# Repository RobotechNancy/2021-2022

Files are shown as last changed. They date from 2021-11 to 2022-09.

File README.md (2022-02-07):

**`ROBOTECH 2021-2022`** 

## **`DÉPÔT OFFICIEL`**  ##

Dépot officiel 2021-2022 de l'équipe Robotech Nancy pour le projet Coupe de France de Robotique

Après de nombreuses années à explorer les quatre coins du monde et de l’univers, nos amis les robots ont

décidé d’aller explorer leur passé. En 2022, les robots iront fouiller les ruines d’une ancienne civilisation robo-
tique à la recherche des fragments oubliés de leurs origines.

Carré de fouille, trésors enterrés et statuettes sacrées, voilà ce qui attend nos archéologues chevronnés, et
rien ne les arrêtera dans la quête de leur Histoire.
Alors sortez les pelles et les pioches, car l’aventure nous attend !

## **`Devise :`** ##
*L’utilsation optimale de l’énergie est une base élémentaire
dans l’ensemble de nos conceptions.
Savoir optimiser l’utilisation des robots existant ne nous satisfait pas.
Nous voulons apprendre à concevoir les robots de demain
utilisant des technologies novatrices ainsi qu’une 
intelligence réelle supportée par une électronique et une informatique de haut niveau.*

Nos objectifs de cette année sont :

- Construire les 2 robots nécessaires dans la version 2022 de la compétition.
- Consolider la structuration en blocs fonctionnels indépendants ( Base roulante, Odométrie, partie robotique annuelle spécifique, Introduction des services de maintenance, … ).
- Rendre les codes informatiques d’un très haut niveau de qualité ( Méthodologique, Fiables ( traitant de toutes erreurs), réelle documentation professionnelle, … ).
- Cette année nous souhaitons introduire les Graphes et moteur de Graphe afin de rendre plus facile et fiable les évolutions de la compétition tant pour cette année et surtout les années à venir.
- Introduire l’utilisation des technologies WEB dans les logiciels d’Interface Homme Robot.
- Consolider les communications hertziennes entre nos deux robots collaboratifs afin d’introduire l'immunité aux attaques de cyber-sécurité.



## **`EQUIPE DE L'ANNEE 2021-2022`**  ##



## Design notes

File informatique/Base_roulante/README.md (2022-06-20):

Sur la Raspy
- fichiers calculDeplacement

Sur STM
- projet STM BR_L432KCU3_V

Pour paramétrer la STM (timer, DMA) et explications générales sur la base roulante voir Rapport_technique_base_roulante

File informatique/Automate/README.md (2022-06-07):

# Ce code permet de :

- Commander un actionneur type servomoteur à angle
- Commander un actionneur type TOR (electroaimant,pompe,etc)
- Commander un actionneur type moteur PAP 

### L'entièreté des codes sont réalisés sur STM32CUBEIDE Version: 1.9.0    Build: 12015_20220302_0855 (UTC) en langage C/C++

### Pour commander un actionneur type servomoteur à angle : 

1. Créer le projet STM sur LA BONNE VERSION de la carte !!
2. Commencer par configurer les pins de la carte sur le .ioc (pin d'envoie de signal et autres si besoin)
> Un servomoteur à angle à besoin en plus du signal d'être (en général) relié à la masse et au 5V (vérifier sur datasheet si la STM suffit pour l'alimenter ou si il faut rajouter une alimentation externe)
3. Regler ensuite les timers pour bien les calibrer (adapter les valeurs des timers en fonction de la valeur de la clock de l'année)
4. Une fois ces 3 actions effectuer, pour faire fonctionner le servomoteur il faut :
    1. Activer la pin configurée précédemment
    2. Régler la valeur du CCR associé au timer en fonctione de l'angle que l'on veut (faire des tests pour trouver la bonne valeur)
    3. Désactiver la pin une fois l'action du servomoteur effectuée
> Attention une fois une commande d'angle lancée, ne pas bloquer et/ou pousser le servomoteur dans le sens inverse cela risque de le casser/dérégler
> Si il y à besoin d'une fonction d'attente, regarder la fonction faite  à la main dans le projet STM et ne pas utiliser la fonction HAL_DELAY de STM, pendant son utilisation, plus rien d'autre ne se passe.

### Pour commander un actionneur type TOR : 

1. Créer le projet STM sur LA BONNE VERSION de la carte !!
2. Commencer par configurer les pins de la carte sur le .ioc (pin d'envoie de signal et autres si besoin)
> Pour un actionneur TOR, il faut configurer dans GPIO output le GPIO mode en Push Pull sans pull-up ni pull-down (voir avec le pole electronique si la carte alimente l'actionneur en push/pull ou en open-drain)
3. Une fois cela configuré, il suffit d'écrire sur la PIN 1 ou 0 (SET ou RESET) pour activer/désactiver l'actionneur (si en open drain, les commandes sont inversées)
> Pour un actionneur TOR, il faudra très souvent brancher l'actionneur sur une alimentation  externe car la STM ne suffira probablement pas

### Pour commander un actionneur type PAP :

Si besoin d'aide supplémentaire sur les  actionneurs, me contacter par mail rey.thibault@orange.fr ou par discord Thibolt#3886 (voir le discord robotech si besoin).

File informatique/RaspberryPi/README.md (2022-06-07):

# Tutoriel pour implémenter un point d'accès sans fil sur une RaspberryPi

##### Utilité du point d'accès :

Le point d'accès d'une RaspberryPi permet de pouvoir créer un réseau sans fil directement sur la carte sans avoir besoin qu'elle se connecte à un partage de connexion distant pour y accéder.

Cette fonction est particulièrement utile lorsqu'on a besoin de se connecter à plusieurs à une RaspberryPi ou lorsqu'on se trouve dans un endroit sans possibilité d'effectuer un point d'accès autre.

```
/!\ Attention : Ce tutoriel ne permet pas d'effectuer le routage de la connexion internet via la RaspberryPi. 
Le point d'accès sans fil ainsi créé ne permettra pas d'accéder à internet ! 

Une solution est de mettre en place un partage de connexion via USB en branchant son téléphone à la RaspberryPi 
via USB et en sélectionnant l'option "Modem USB" dans les paramètres de connexion.
```

##### Mise en place du point d'accès :

On vérifie tout d'abord que le système est bien à jour, et on installe les paquets nécessaires :

```bash
sudo apt update -y && sudo apt upgrade -y 
```
```bash
sudo apt install hostapd dnsmasq -y
```

On effectue ensuite les configurations nécessaires :

```bash
sudo systemctl stop hostapd dnsmasq
```

```bash
sudo nano /etc/hostapd/hostapd.conf
```

On ajoute le code suivant à la fin du fichier :
```
interface=wlan0
driver=nl80211
ssid=robotechnancygrand
hw_mode=g
channel=7
wmm_enabled=0
macaddr_acl=0
auth_algs=1
ignore_broadcast_ssid=0
wpa=2
wpa_passphrase=Robotech2022@
wpa_key_mgmt=WPA-PSK
wpa_pairwise=TKIP
rsn_pairwise=CCMP
```

```bash
sudo systemctl unmask hostapd && sudo systemctl enable hostapd
```

```bash
sudo nano /etc/default/hostapd
```

On décommente la ligne et on la complète comme ceci :

```
DAEMON_CONF="/etc/hostapd/hostapd.conf"
```

```bash
sudo nano /etc/dnsmasq.conf
```

On ajoute le code suivant à la fin du fichier :

```
interface=wlan0
domain-needed
bogus-priv
dhcp-range=192.168.50.150,192.168.50.200,255.255.255.0,12h
```

```bash
sudo nano /etc/dhcpcd.conf
```

On ajoute le code suivant à la fin du fichier :

```
interface wlan0
nohook wpa_supplicant
static ip_address=192.168.50.10/24
static routers=192.168.50.1
```

On redémarre la RaspberryPi :

```bash
sudo reboot
```

##### Connexion au point d'accès :

- Connexion au wifi généré par la RaspberryPi **[mot de passe : Robotech2022@]**
- Connexion en ssh
```
ssh pi@192.168.50.10 
```
**[mot de passe : robotech2022]**

##### Désactivation du point d'accès :

```bash
sudo nano /etc/dhcpcd.conf
```

Commenter les lignes suivantes (à la fin du fichier) :

```bash
#interface wlan0
#nohook wpa_supplicant
#static ip_address=192.168.50.10/24
#static routers=192.168.50.1
```

On désactive les services réseaux :

```bash
sudo systemctl disable dnsmasq hostapd
```

On redémarre la RaspberryPi :

```bash
sudo reboot
```

##### Réactivation du point d'accès :

```bash
sudo nano /etc/dhcpcd.conf
```

Décommenter les lignes suivantes (à la fin du fichier) :

```bash
interface wlan0
nohook wpa_supplicant
static ip_address=192.168.50.10/24
static routers=192.168.50.1
```

On réactive les services réseaux :

```bash
sudo systemctl enable dnsmasq hostapd
```

On redémarre la RaspberryPi :

```bash
sudo reboot
```

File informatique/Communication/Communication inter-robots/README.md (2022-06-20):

# Le code permet de réaliser :

- la communication inter-robots via XBee (envoi/réception de trames)
- le paramétrage des modules XBee en UART via le port GPIO de la RaspberryPi 

> *Remarque :* Tous les codes sont écrits en style **C/C++**

# Format de la trame des messages envoyés et reçus :

|Début de trame|Adr_emetteur|Adr_destinataire|Id_trame|Nb octets msg|Code_fonction|Paramètres|CRC16 Modbus|Fin de trame|
|:---:|:---:|:---:|:---:|:---:|:---:|:---:|:---:|:---:|
|*1 octet*|*1 octet*|*1 octet*|*2 octets*|*1 octet*|*1 octet*|*<255 octets*|*2 octets*|*1 octet*|
|STX|0xXX|0xXX|0xXX 0xXX|0xXX|0xXX|DATA|0xXX 0xXX|EOT|

> *Remarque :* Tous les codes et adresses nécessaires pour la trame sont définis dans le fichier **#xbee_define.h**

# Principales caractéristiques des connexions mises en oeuvre :

|Nom de la communication|Vitesse de transfert|Portée|Type de communication|Caractéristiques de transmission utilisés (série)|Bande(s) de fréquence
|:---:|:---:|:---:|:---:|:---:|:---:|
|Module XBee type S1|RF : 250Kbps - série: jusqu'à 250Kbps|60m (intérieur) - 90m (extérieur)|Sans fil - Haute Fréquence|9600 bauds - Bit de parité pair - 1 bits de stop - 8 bits de data - chiffrement AES 128 Bits|2,4 GHz avec étalement de spectre|
|Liaison UART|9600 - 115200 bauds|/|Filaire|9600 bauds - Bit de parité pair - 1 bits de stop - 8 bits de data|/|

> Plus d'informations sur le module Digi Xbee 3 DigiMesh 2.4 RF [ici](https://www.digi.com/products/embedded-systems/digi-xbee/rf-modules/2-4-ghz-rf-modules/xbee3-digimesh-2-4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), sur le module XBee S1 [ici](https://www.digi.com/resources/documentation/Digidocs/90000982/Default.htm) ou directement sur la [datasheet du module](https://www.digi.com/resources/library/data-sheets/ds_s2c-xbeedigimesh-24)

# Installation du code (sous Linux x86-64) :

```bash
git clone https://github.com/RobotechNancy/2021-2022.git
```

[**Username** : votre nom d'utilisateur GitHub] 

[**Password** : vous devez générer un personal access token dans `Github -> Settings -> Developer Settings -> Personal Access Token -> Generate new token`]

```bash
cd 2021-2022/Pôle\ informatique/Communication/Communication\ inter-robots/xbee/  

g++ *.cpp -std=c++17 -pthread -o output

./output
```

# Publication d'une nouvelle version du code (sous Linux x86-64) :

```bash
git pull && git add * && git commit -m "Version XX.XXR" && git push
```

[**Username** : votre nom d'utilisateur GitHub] 

[**Password** : vous devez générer un personal access token dans `Github -> Settings -> Developer Settings -> Personal Access Token -> Generate new token`]

# Câblage des modules XBee avec la RaspberryPi

### Points de vigilance :

- L'alimentation de la RaspberryPi, pour une RaspberryPi3B+ ou modèle antérieur : 5.5V / 2A max. (utilisez une alimentation de la salle C244)
> une sous-alimentation entraine une dégradation notoire de la communication UART : ne pas utiliser de chargeur de téléphone (même charge rapide) !

> un câble USB/Micro USB de mauvaise qualité entraine un fonctionnement erroné

- Le câblage du module XBee :
> ne pas utiliser les 4 pins situés à l'arrière de l'[adaptateur XBee vers DIM](./images/adaptateur_xbee.jpg) -> utiliser les pins situés sur le dessous du support **uniquement**

> vérifier le [GPIO Pinout Diagram](https://pinout.xyz) de votre modèle de Raspberry

> les modules XBee s'alimentent en 3,3V

- La compatibilité entre les modules XBee :
> 2 modules XBee ne sont compatibles que s'ils sont du même type (par ex. les modules XBee S1 et XBee S2C ne sont pas compatibles entre eux)

- En cas d'impossibilité d'accès au module XBee et pour vérifier s'il n'est pas endommagé :
> utiliser le logiciel propriétaire [XCTU](http://www.digi.com/xctu) et connecter le module XBee au port USB de votre ordinateur à l'aide de l'[explorer board XBee](./images/explorer_xbee.jpg)

> dans le logiciel XCTU, cliquez sur l'icône avec la loupe et non celui avec le + pour ajouter un module

- Si vous rencontrez un autre problème, la **meilleure** solution est d'utiliser [un analyseur numérique de signal (ou un oscilloscope)](./images/oscilloscope.jpg), notamment les oscilloscopes digitaux Rohde & Schwarz de la salle C244

### Schéma de câblage :

- Câblage RaspberryPi 3B + Xbee S1 :

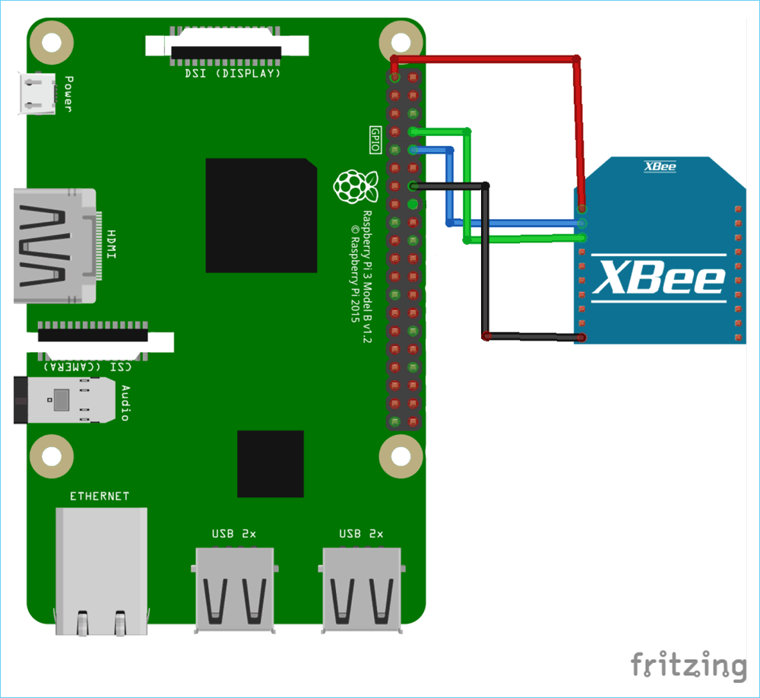
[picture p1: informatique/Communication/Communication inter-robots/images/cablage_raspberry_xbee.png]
Câblage RaspberryPi 3B + Xbee S1


- GPIO Pinout Xbee S1 :

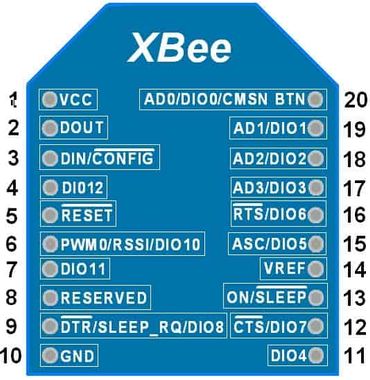
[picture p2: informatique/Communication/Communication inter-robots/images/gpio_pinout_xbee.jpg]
GPIO Pinout Xbee


|**PIN**|**DESCRIPTION**|
|:---:|:---:|
|1|**Alimentation (3,3V)**|
|2|**UART Tx**|
|3|**UART Rx**|
|4|Digital output 8|
|5|Module RESET (pulse reset min. 200ns)|
|6|PWM sortie 0|
|7|PWM sortie 1|
|8|*Ne pas connecter*|
|9|STR / Digital input 8|
|10|**Masse (GND)**|
|11|Analog input 4 / Digital I/O 4|
|12|Clear-to-Send Flow control / Digital I/O 7|
|13|Indicateur d'état du module|
|14|Tension de référence pour les entrées A/D|
|15|Associated Indicator / Analog Input 5 / Digital I/O 5|
|16|Request-to-Send Flow Control / Analog Input 6 / Digital I/O 6|
|17|Analog Input 3 or Digital I/O 3|
|18|Analog Input 2 or Digital I/O 2|
|19|Analog Input 1 or Digital I/O 1|
|20|Analog Input 0 or Digital I/O 0|

- GPIO Pinout RaspberryPi 3B :

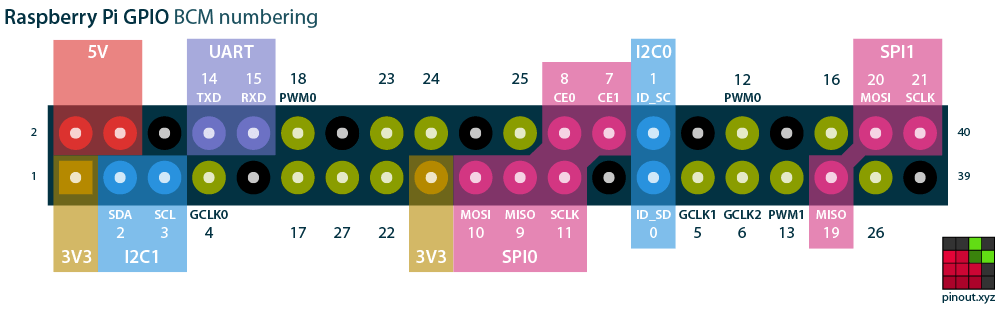
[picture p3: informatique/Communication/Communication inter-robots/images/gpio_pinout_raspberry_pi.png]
GPIO Pinout RaspberryPi


> Les pins dessinés en noir non légendés représentent la masse commune de la Raspberry

- Cablâge ArduinoUno + XBee S1 :

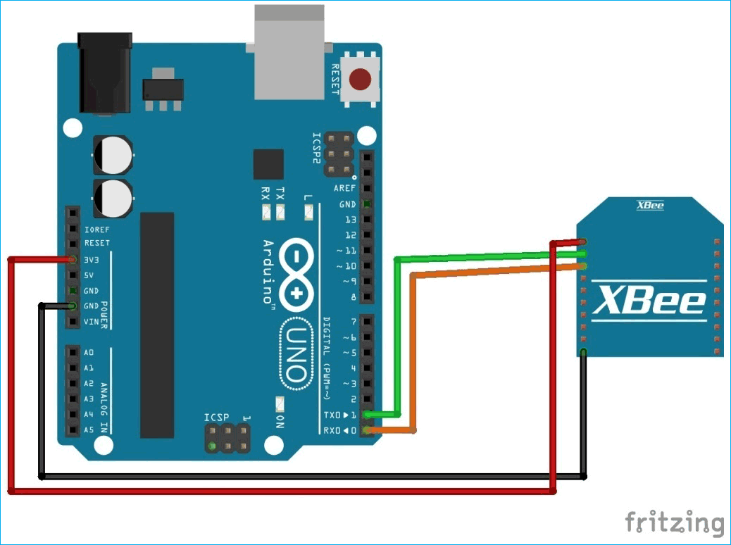
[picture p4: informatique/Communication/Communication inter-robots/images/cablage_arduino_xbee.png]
Cablâge ArduinoUno + XBee S1


# Documentation du code :

- toute la documentation a été générée grâce à l'outil [Doxygen](https://www.doxygen.nl/index.html)
- le fichier de configuration de Doxygen se trouve dans le dossie **xbee** (fichier *Doxyfile*)
- pour consulter la documentation en PDF, ouvrer le fichier **refman.pdf** situé dans le dossier `doc -> latex -> refman.pdf`
- pour consulter la documentation en HTML, ouvrer le fichier **index.html** situé dans le dossier `doc -> html -> index.html`

***
En cas de besoin, contactez moi sur Discord `@heatsink.ru#1183` ou par mail samueldittedestree@protonmail.com

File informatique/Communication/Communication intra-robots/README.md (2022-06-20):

# definition de la trame du bus can

## Champ d'identification en version étendu (29 bit)
| msg urgent | desitnataire | emetteur | code fct |  id msg  | reponse ou question | id rep |
| --- | --- | --- | --- | --- | --- | --- |
| 0 | 0001 | 0010 | 00000101 | 00000001 | 0 | 001  |

- msg urgent : 0 pour un message urgent, 1 sinon
- destinataire : addresse du destinataire du message sur 4 bit (0 à 15)
- emetteur : addresse de l'emetteur du message sur 4 bit (0 à 15)
- code fonction : code fonction du message qui indique a quoi sert le message sur 8 bit (0 à 254)
- id du message : identique entre une demande et une reponse ce qui permet d'idnetifier la réponse, sur 8 bit (0 à 254)
- reponse ou question : un bit , 1 pour une reponse et 0 sinon
- id rep : si des donners doivent etre transmis sur plusieur trame

dans le bus can la prioriter des messages en cas de conflit est donner au message avec le champ d'identification le plus faible.
>ceci implique que les messages sont priorisé par le déstinataire du message

### Adresse des cartes 21-22
| adresse | carte |
| :---: | :---: |
| 1 | raspberry pi |
| 2 | base roulante |
| 3 | odometrie |
| 4 | actionneur |
| 5 | pi zero |
>la pi zero n'a pas était implementé cette année 

# Mise en place du bus can
## Sur la raspberry

installer le packet can-utils : 
```bash
sudo apt install can-utils
```

ajouter le fichier `/boot/config.txt` :
```bash
dtoverlay=mcp2515-can0,oscillator=12000000,interrupt=25,spimaxfrequency=2000000
```
12000000 dépend du quartz utilisé (souvent 12000000 ou 8000000)

il faut lancer cette commande a chaque redémarage de la raspberry :
```bash
sudo ip link set can0 up type can bitrate 181818 loopback off
```
- le bitrate doit etre le meme sur toute les cartes du bus can
- il est possible de passer en **loopback on** ce qui fait que les messages **NE sont PLUS** envoyer dans le bus can mais sont renvoyer sur la carte.
- pour arreter le bus can (et pouvoir le redmarer avec d'autre parametre) : `sudo ip link set can0 down`

## Sur une STM32

Dans le .ioc :
- activer le bus **can1** ou **can**
- dans **Parameter Settings** modifier :
	- **Prescaler (for Time Quantum)**
	- **Time Quanta in Bit Segment 1**
	- **Time Quanta in Bit Segment 2**
de tel sorte d'obtenir le **Baud Rate** voulu (identique autre carte connecter au bus can. 181818 bit/s par example).
Sur une carte en confguration par default :

| PARAMETRE | VALEUR |
| --- | --- |
| **Prescaler (for Time Quantum)** | 16 |
| **Time Quanta in Bit Segment 1** | 8 Times | 
| **Time Quanta in Bit Segment 2** | 2 Times | 

- dans **NVIC Settings** tous cocher !!! (4 cases ou 1 en fonction de la carte)
- verifier que les pin sont bien ascossier comme cela :

| PIN  | DESCRIPTION |
| --- | --- |
| PA12 | CAN1_TX |
| PA11 | CAN1_RX | 
- Inclure les fichiers : can.c, can.h, defineCan.h
- dans le main :
	- include `#include "defineCan.h"` et `#include "can.h"`
	- dans le user code 2 du main mettre 
```c
CAN_Config(hcan1, CAN_ADDR_BASE_ROULANTE_E);
``` 
avec hcan1 la variable de type `CAN_HandleTypeDef` instantier dans private variable, et **CAN_ADDR_BASE_ROULANTE_E** une valeur de l'enum **CAN_EMIT_ADDR**

# Utilisation du bus can
## Sur la raspberry
il existe un certain nombre de commande qui permete d'utilise le bus can :
- **candump can0** permet d'afficher tous les messages qui passe sur le bus can (meme ceux envoyer par la raspberry)
> si les messages envoyer n'apparaissent c'est qu'il n'y a aucune autre carte sur le bus pour accuser reception -> problème de branchement, !! resistance entre canL et canH !!
> si les messages envoyer apparaissent en double -> le loopback est activer, les messages ne sont pas envoyé aux autres cartes

- **cansend can0** permet d'envoyer un messages sur le bus can :
> example de syntaxe : `cansend can0 03132010#12`
> pour information sur l'utilisation de la commande : `cansend` ou `man cansend`

- la librairie possede un grand nombre d'autre commande [cf .doc du packet](https://github.com/linux-can/can-utils)

librairie orienté objet en c++ : voir le dossier [can_raspberry](https://github.com/RobotechNancy/2021-2022/edit/main/P%C3%B4le%20informatique/Communication/Communication%20intra-robots/can_raspberry/)

## Sur une STM32
les messages reçu déclanche une intéruption en appelant la fonction 
```c
void HAL_CAN_RxFifo0MsgPendingCallback(CAN_HandleTypeDef *hcan)
```
pour envoyer un message il faut utiliser 
```c
int send(CAN_ADDR addr, CAN_CODE_FCT codeFct , uint8_t data[], uint dataLen, bool isRep, uint repLenght, uint idMessage)
```

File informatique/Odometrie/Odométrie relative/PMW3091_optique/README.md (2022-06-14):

/////////////////////////////////////////////////////// Utilisation code CAPTEUR OPTIQUE PMW3091 ///////////////////////////////////////////////////////

## DRIVERS : PMW3091.c et PMW3091.h

- Le .c contient les fonctions utilent pour faire fonctionner le capteur correctement et dans le .h on annonce chaque fonction
- Les deux doivent être implémentés dans le projet sous forme de Source Folder
- Il faut ajouter en include les drivers pour que ça marche

## STM32L432K : PMW3091.ioc

- Pour faire fonctionner le reste du code : le port SPI sur la carte STM 32 doit être activé manuellement sur l'IDE de STM 32 en FULL Duplex Master
- ACtiver sur la STM32 les ports SPI1_SCK et en plus un port GPIO_OUTPUT : qu'il faut renommer SPI1_CS
- Au niveau de la connectivité SPI de la carte STM il faut aller dans parameter Settings => 

  - Frame Format : Motorola
  - Data Size : 8 Bits
  - First Bit : MSB First
  - Prescaler (for Baud Rate) : 256
  - Baud Rate : 125 Kbits/s
  - Clock Polarity : Low
  - Clock Phase : 1 Edge
  - CRC Calculation : Disabled
  - NSSP Mode : Enabled 
  - NSS Signal Type : Software
 
 ## Main : main.c 
 
 - Il faut ajouter le PMW3091.h en include
 - Il faut d'abord initialiser le capteur dans le code grâce à la fonction qui le permet (PMW3901_Status_t PMW3901_Init(PMW3901_Descriptor_t *_Descriptor))
 - Si l'initialisation fonctionne les leds du capteur devrait s'allumer
 - Ensuite il faut ajouter la fonction permettant de lire la variation de position du capteur (PMW3901_Status_t PMW3901_Read_Variation(int16_t *var_x, int16_t *var_y))

 ## Résumé 
 
 Le code présent déjà sur le Git permet actuellement de faire fonctionner le capteur optqiue c'est à dire qu'en installant l'application putty et en lancant en parallèle le code, on récupère la variation en x et en y du déplacement du capteur en mm grâce à deux DEFINE qui convertissent les données reçues en mm.
 
 De plus, il permet ensuite de calculer la position relative du capteur : c'est à dire que si le robot bouge il va garder en position initiale l'endroit où il était au démarrage du code et ensuite on le déplacant, on observera sur putty en mm les longueurs qu'il aura parcouru. En le remettant à la position initiale il va redonner posX = 0 et posY = 0 avec un taux d'erreur de lordre du mm.
 
 Le code fonctionne pour les 2 robots que ce soit pour le capteur du petit robot tout comme celui du grand robot. La seule chose qu'il faut modifier entre le petit et le grand robot, c'est les DEFINE en haut du code correspondant au coefficient en X et en Y qu'on doit modifier afin d'ajuster la position du capteur en relatif (directement par rapport au robot).
 
 Lien vers la DATASHEET : 
[Datasheet_CapteurOptique_PMW3901 (2).pdf](https://github.com/RobotechNancy/2021-2022/files/8897904/Datasheet_CapteurOptique_PMW3901.2.pdf)


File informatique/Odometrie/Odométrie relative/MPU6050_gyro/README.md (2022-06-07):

# Le code permet de réaliser :

- la communication en I2C avec le gyroscope
- l'initialisation du gyroscope
- la récupération de la vitesse angulaire, et sa conversion en angle de rotation sur l'axe Z (axe à la verticale du capteur lorque ce dernier est posé à l'horizontal)

> *Remarque :* Le code contenu dans le fichier GYRO_ACC_SAM est l'ensemble du projet réalisé sur l'**IDE STM32** | /!\ Le code **ne permet pas** l'utilisation de l'accéléromètre intégré au capteur

# Utilisation du code :

Pour utiliser le code, il vous faut :

- une carte STM32 disposant au minimum d'un bus I2C et d'une Pin d'interruption
  > le modèle utilisé pour le projet est la STM32L432KCU3 : pour utiliser la librairie sur une autre carte, copier uniquement les fichiers **Core/Inc/Gyro.h**, **Core/Inc/MPU6050.h**, **Core/Src/Gyro.c** ainsi que **Core/Src/MPU6050.c** et créer un nouveau projet STM
  >
- un gyrocope de type MCU6050
  > attention : pour câbler correctement le module, référez-vous à la section ci-après
  >
- avoir installé (sur windows ou linux) l'IDE fourni par STM32 appelé STM32CUBEIDE (disponible [ici](https://www.st.com/en/development-tools/stm32cubeide.html))
- des câbles de connexion et une plaque d'essai (ou un shield adapté)

Les fichiers **Core/Inc/Gyro.h**, **Core/Inc/MPU6050.h**, **Core/Src/Gyro.c** ainsi que **Core/Src/MPU6050.c** ont été écrit à la main, et servent à la configuration du capteur pour notre utilisation. Il se peut que vous soyez ammenés à les modifier, donc voici une courte description de chacun d'entre eux :
  
-> Dossier **Core/Inc** :

- le fichier "*MPU6050.h*" contient le code permettant de configurer les paramètres utilisés pour comminiquer avec le capteur et récupérer les valeurs, et permet également d'inclure la librairie associée à la famille de la carte en cours d'utilisation.

Au début du fichier, on trouve :

```
  #include "stm32l4xx_hal.h"
```

   Pour une autre famille de carte, il suffit de remplacer cette ligne, et de mettre le nom de la famille de la carte. Vous pouvez trouver cette information en regardant le nom du fichier de votre projet situé dans "**Core/Inc/stm32XXXX_hal_conf.h**". Recopier ce nom (sans le *_conf*) dans le fichier à la ligne citée précédemment.
   
  Le reste du fichier contient la configuration du module, avec notamment la posibilité de modifier sa sensibilité, sa vitesse d'horloge, sa fréquence et ses paramètres d'interruptions. Toutes les configurations possibles pour ces paramètres se trouvent *dans les énum des lignes 27 à 119*.  
  
  On trouve ensuite les paramètres en cours d'utilisation, sous forme de 3 structures, situées *entre les lignes 121 et 149*. 
  
  Enfin, on trouve les prototypes des fonctions qui permettent d'initialiser le capteur, et de récupérer la vitesse angulaire fournie par le capteur. Cette vitesse sera ensuite utilisée et traitée par le fichier **Gyro.c**.
  
- le fichier "*Gyro.h*" contient les prototypes des fonctions permettant de gérer la calibration du capteur ainsi que la conversion et le traitement des valeurs de vitesse angulaire afin de fournir la rotation en degrés.  

-> Dossier **Core/Src** :

- le fichier "*MPU6050.c*" contient les fonctions qui permettent d'initialiser le capteur, et de récupérer la vitesse angulaire fournie par le capteur.  

- le fichier "*Gyro.c*" contient les fonctions permettant de gérer la calibration du capteur ainsi que la conversion et le traitement des valeurs de vitesse angulaire afin de fournir la rotation en degrés. Ce fichier est une extension des fonctions contenues dans "*MPU6050.c*", d'où l'inclusion du fichier dans la classe *Gyro*.

Afin d'asssurer le fonctionnement de la librairie, il est nécessaire de modifier légèrement le fichier "*Core/Src/stm32l4xx_it.c*", afin d'ajouter dans la liste des include la libairie `#include "MPU6050.h"`. Il faut également appeler la fonction "*MPU6050_Interrupt_Routine()*" dans la fonction d'interruption système (située à la fin du fichier), pour obtenir un résultat comme ceci :

```c
/**
  * @brief This function handles EXTI line[9:5] interrupts.
  */
void EXTI9_5_IRQHandler(void)
{
  /* USER CODE BEGIN EXTI9_5_IRQn 0 */

  /* USER CODE END EXTI9_5_IRQn 0 */
  HAL_GPIO_EXTI_IRQHandler(GPIO_PIN_6);
  /* USER CODE BEGIN EXTI9_5_IRQn 1 */
  MPU6050_Interrupt_Routine();
  /* USER CODE END EXTI9_5_IRQn 1 */
}
```
> *Remarque :* Les numéros des fonctions par défaut dépendant de la carte utilisée et de la configuration mise en place, et sont donc susceptibles de changer

# Câblage des modules et pinout configuration

Voici le câblage utilisé pour le projet, utilisant 1 capteur MPU6050 et une carte STM32L432KCU3 :

| MPU6050 | STM32L432KCU3 |
| --- | --- |
| GND (masse) | GND (pin CN4-2 ou pin CN3-4) |
| SCL (serial clock) | PA9 |
| SDA (serial data)  | PA10 |
| VIN (alimentation) | +3.3V (pin CN4-14) |

*Les pins situés sur la même ligne sont reliés entre eux*

> Pour configurer le bus I2C sur la carte STM32, il faut penser à activer les réglages de l'interruption du bus, dans le fichier **IOC du projet STM32**, dans le menu **Connectivity>I2C1>NVIC Settings** et cocher l'activation des interruptions **I2C1 event interrupt** et **I2C1 error interrupt** . Il faut ensuite se rendre dans le menu **System Core>GPIO>I2C** et de modifier les 2 lignes du bus I2C en réglant la valeur de **GPIO Pull-Up/Pull-down** sur **Pull-up** (il suffit de double cliquer sur chacune des deux lignes pour faire apparaitre le menu).
>
> Cela permet de ne pas mettre de résistances de Pull-up aux extrémités du bus I2C puisqu'elles sont en réalité internes dans la carte STM32.
> Le mode de l'I2C à utiliser est *I2C*
> Il faut ensuite utiliser une Pin non utilisée (PA6 sur l'IOC dans notre projet) et la régler sur "*GPIO_EXTI6*" afin de l'utiliser par la suite comme Pin d'interruption

Pinout configuration de la carte STM32 NUCLEO-L432KCU3 :

| Numéro de la PIN  | CN3 (partie gauche de la carte) | CN4 (partie droite de la carte) |
| --- | --- | --- |
| 1 | PA9 - D1 (SCL) | VIN |
| 2 | PA10 - D0 (SDA) | GND (masse) |
| 3 | NRST | NRST |
| 4 | GND (masse) | +5V |
| 5 | PA12 - D2 | PA2 - A7 |
| 6 | PB0 - D3 | PA7 - A6 |
| 7 | PB7 - D4 | PA6 - A5 |
| 8 | PB6 - D5 | PA5- A4 |
| 9 | PB1 - D6 | PA4 - A3 |
| 10 | PC14 - D7 | PA3 - A2 |
| 11 | PC15 - D8 | PA1 - A1 |
| 12 | PA8 - D9 | PA0 - A0 |
| 13 | PA11 - D10 | AREF |
| 14 | PB5 - D11 | +3.3V |
| 15 | PB4 - D12 | PB3 - D13 |

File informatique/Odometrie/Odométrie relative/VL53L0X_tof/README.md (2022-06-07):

# Le code permet de réaliser :

- la communication en I2C avec les capteurs TOF
- l'initialisation des capteurs un à un
- la lecture et la conversion des valeurs afin de récupérer des valeurs de distances mesurées en mm

> *Remarque :* Le code contenu dans le fichier TOF_SAM est l'ensemble du projet réalisé sur l'**IDE STM32**

# Utilisation du code :

Pour utiliser le code, il vous faut :

- une carte STM32 disposant au minimum d'un bus I2C et d'un GPIO
  > le modèle utilisé pour le projet est la STM32L432KCU3 : pour utiliser la librairie sur une autre carte, copier uniquement le dossier **Drivers/VL53L0X** et le contenu ***utilisateur*** du fichier **Core/Src/main.c** et créer un nouveau projet STM
  >
- un ou plusieurs capteurs TOF de type VL53L0X (ou VL53LXX)
  > attention : pour câbler correctement les modules, référez-vous à la section ci-après
  >
- avoir installé (sur windows ou linux) l'IDE fourni par STM32 appelé STM32CUBEIDE (disponible [ici](https://www.st.com/en/development-tools/stm32cubeide.html))
- des câbles de connexion et une plaque d'essai

Ce code est basé sur la librairie STM32 qui a été adaptée de manière à être universelle pour toutes les cartes compatibles. La librairie modifiée se trouve dans le dossier **Drivers/VL53L0X.**

Les dossiers **Src** et **Inc** contiennent uniquement des fichiers générés par STM, il ne faut surtout pas les modifier.

Les fichiers commencant par **"TOF_"** et situés dans les dossiers **Implementation** et **Platform** ont été écrit à la main, et servent à l'implémentation du code pour notre utilisation. Il se peut que vous soyez ammenés à les modifier, donc voici une courte description de chacun d'entre eux :

-> Dossier **Implementation** :

- le fichier "*TOF_STM_Reference.h*" contient uniquement le code permettant d'inclure la librairie associée à la famille de la carte en cours d'utilisation.

  ```
  #include "stm32l4xx_hal.h"
  ```

    Pour une autre famille de carte, il suffit de remplacer cette ligne, et de mettre le nom de la famille de la carte. Vous 			pouvez trouver cette information en regardant le nom du fichier de votre projet situé dans "**Core/Inc/stm32XXXX_hal_conf.h**". Recopier ce nom (sans le *_conf*) dans le fichier cité précédemment.

- le fichier "*TOF_STM_Units.h*" contient les informations par défaut des capteurs (adresse I2C, ID de base, mode de relevé de mesure, ...) ainsi que la liste des noms de capteurs TOF utilisés sous forme d'une structure de type *enum*.

  ```
  typedef enum {
  	TOF_UNIT_0 = 0,
  	TOF_UNIT_1 = 1,

  	TOF_UNIT_COUNT // Let this enum value !!!! Mandatory for the driver operations
  } TOF_Units_t;
  ```

    Dans notre exemple, il y deux capteurs TOF listés qui s'appellent respectivement*TOF_UNIT_0* et *TOF_UNIT_1* et qui possèdent les numéros 0 et 1. Pour ajouter un modèle, il suffit de le mettre dans cette liste, et dans le fichier "*TOF_STM_Units.c*" associé.

- le fichier "*TOF_STM_Units.c*" contient les informations détaillées de la liste des capteurs TOF du fichier précédent.
  ```
  VL53L0X_Dev_t TOF_Devices[] = {
  	{
  		.Id = TOF_UNIT_0,
  		.I2cHandle = &hi2c1,
  		.XSHUT_Port = TOF0_XSHUT_GPIO_Port,
  		.XSHUT_Pin = TOF0_XSHUT_Pin
  	},
  	{
  		.Id = TOF_UNIT_1,
  		.I2cHandle = &hi2c1,
  		.XSHUT_Port = TOF1_XSHUT_GPIO_Port,
  		.XSHUT_Pin = TOF1_XSHUT_Pin
  	}
  };
  ```

    Pour chaque module listé dans le fichier .h, on retrouve son ID, l'ID de l'objet I2C (du bus I2C) auquel il est connecté, le nom du port GPIO auquel est connecté la sortie XSHUT du capteur, ainsi que le nom de la Pin qui lui est associée. Pour ajouter un module, il suffit de respecter le format en incrémentant le numéro que le dernier TOF listé possède dans chacune des variables (le même bus I2C étant utilisé pour tous les capteurs, cette variable ne change pas).

> *Remarque importante :* Les capteurs TOF VL53L0X ne possèdent que de la mémoire volatile, et ne retiennent donc pas la nouvelle adresse de bus I2C qui leur est associée. Par défaut, tous les capteurs ont la même adresse, à chaque démarrage, il faut donc tous les éteindre, puis les allumer un à un et leur attribuer une adresse différente entre eux pour pouvoir les distinguer et commiquer avec un à un. C'est tout l'intérêt de la sortie XSHUT du capteur qui signifie XSHUTDOWN, et qui permet d'éteindre les capteurs un à un via le port GPIO de la STM lors de l'initialisation.

    Pour que l'ensemble du code fonctionne, il faut donc que chaque capteur TOF soit relié à une Pin GPIO différente sur la carte STM32. Pour configurer les Pins GPIO sur la carte, il faut repérer sur la carte des Pins non utilisées (*voir la section du câblage pour plus d'informations*), puis se rendre dans le fichier **.ioc** du projet STM32, clic droit sur la Pin choisie, puis sélectionner "GPIO Output" dans la liste déroulante des options. La Pin passe alors à l'état activé et se colore en vert. Il faut ensuite éditer son nom, en effectuant un clic gauche sur la Pin, puis sélectionner "Enter User Label" et indiquer le nom de la Pin sous la forme "TOFX_XSHUT", où le premier X désigne le numéro choisi pour le capteur dans la liste du fichier précédent.

-> Dossier **Platform** :

- le fichier "*TOF_Errors.h*" contient la liste de l'ensemble des codes erreurs qui peuvent être utilisés dans toute la librairie. Leurs noms sont assez explicites, et si on effectue un *Ctrl+clic droit* sur chacune des variables, on peut trouver un commentaire descriptif de l'erreur. Toutefois, si vous souhaitez des descriptions plus précises, vous pouvez consulter le site suivant : [https://documentation.help/VL53L0X-API/](https://documentation.help/VL53L0X-API/)
- le fichier "*TOF_Types.h*" contient les listes des options utilisables pour modifier les paramètres des capteurs, comme le mode de relevé de valeurs, ou encore l'état du capteur.
- les fichiers "*TOF.h*" et "*TOF.c*" contiennent les deux fonctions principales qui sont utilisables par l'utilisateur de la librairie, une première qui permet d'initialiser les capteurs TOF, en paramétrant les registres, et les adresses I2C de chaque capteur, et une seconde qui permet d'effectuer un relevé de la distance fournie par un capteur en mm. D'autres fonctions sont également présentes et sont des fonctions utilitaires internes qui servent aux deux fonctions principales pour mieux découper le programme.

  > Par défaut, les relevés de mesure s'effectuent en mode "LONG_RANGE"
  >

L'ensemble de cette librairie est utilisée dans le fichier **Core/Src/main.c** qui permet d'appeler les fonctions de la librairie, d'initialiser les capteurs, de lire les valeurs envoyées par les capteurs et de transmettre ces valeurs via le bus UART à l'utilisateur afin qu'il puisse vérifier qu'elles sont cohérentes (une valeur de statut est également envoyée à chaque mesure, afin d'indiquer si cette dernière a correctement été effectuée).

# Câblage des modules et pinout configuration

Voici le câblage utilisé pour le projet, utilisant 2 capteurs TOF et une carte STM32L432KCU3 :

| VL53L0X n°1 | VL53L0X n°2  | STM32L432KCU3 |
| --- | --- | --- |
| XSHUT | / | PA6 |
| / | XSHUT | PA5 |
| GND (masse) | GND | GND (pin CN4-2 ou pin CN3-4) |
| SCL (serial clock) | SCL | PA9 |
| SDA (serial data)  | SDA | PA10 |
| VIN (alimentation) | VIN | +3.3V (pin CN4-14) |

*Les pins situés sur la même ligne sont reliés entre eux*

> Pour configurer le bus I2C sur la carte STM32, il faut penser à changer les réglages de la vitesse, dans le fichier **IOC du projet STM32**, dans le menu **Connectivity>I2C1>Parameter Settings** et régler la valeur de **I2C Speed Frequency (KHz)** à 10 (au lieu de 100 par défaut). Il faut ensuite se rendre dans le menu **System Core>GPIO>I2C** et de modifier les 2 lignes du bus I2C en réglant la valeur de **GPIO Pull-Up/Pull-down** sur **Pull-up** (il suffit de double cliquer sur chacune des deux lignes pour faire apparaitre le menu).
>
> Cela permet de ne pas mettre de résistances de Pull-up aux extrémités du bus I2C puisqu'elles sont en réalité internes dans la carte STM32.

Pinout configuration de la carte STM32 NUCLEO-L432KCU3 :

| Numéro de la PIN | CN3 (partie gauche de la carte) | CN4 (partie droite de la carte) |
| --- | --- | --- |
| 1 | PA9 - D1 (SCL) | VIN |
| 2 | PA10 - D0 (SDA) | GND (masse) |
| 3 | NRST | NRST |
| 4 | GND (masse) | +5V |
| 5 | PA12 - D2 | PA2 - A7 |
| 6 | PB0 - D3 | PA7 - A6 |
| 7 | PB7 - D4 | PA6 - A5 |
| 8 | PB6 - D5 | PA5- A4 |
| 9 | PB1 - D6 | PA4 - A3 |
| 10 | PC14 - D7 | PA3 - A2 |
| 11 | PC15 - D8 | PA1 - A1 |
| 12 | PA8 - D9 | PA0 - A0 |
| 13 | PA11 - D10 | AREF |
| 14 | PB5 - D11 | +3.3V |
| 15 | PB4 - D12 | PB3 - D13 |

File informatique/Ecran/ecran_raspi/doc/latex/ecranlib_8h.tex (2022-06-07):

\hypertarget{ecranlib_8h}{}\doxysection{Référence du fichier ecranlib.\+h}
\label{ecranlib_8h}\index{ecranlib.h@{ecranlib.h}}

Fichier d\textquotesingle{}en-\/tête de la classe \mbox{\hyperlink{class_ecran}{Ecran}}. Cette classe est utilisée afin de communique en UART avec l\textquotesingle{}écran sur la Raspberry\+Pi.  

{\ttfamily \#include \char`\"{}ecran\+\_\+define.\+h\char`\"{}}\newline
{\ttfamily \#include \char`\"{}serialib.\+h\char`\"{}}\newline
{\ttfamily \#include \char`\"{}loglib.\+h\char`\"{}}\newline
{\ttfamily \#include $<$string$>$}\newline
{\ttfamily \#include $<$iomanip$>$}\newline
{\ttfamily \#include $<$iostream$>$}\newline
{\ttfamily \#include $<$chrono$>$}\newline
{\ttfamily \#include $<$thread$>$}\newline
{\ttfamily \#include $<$iterator$>$}\newline
\doxysubsection*{Classes}
\begin{DoxyCompactItemize}
\item 
struct \mbox{\hyperlink{struct_trame__t}{Trame\+\_\+t}}
\item 
class \mbox{\hyperlink{class_ecran}{Ecran}}
\begin{DoxyCompactList}\small\item\em Cette classe est utilisée pour la communication entre un ecran STM32\+F7G et une Raspberry\+Pi. \end{DoxyCompactList}\end{DoxyCompactItemize}

\doxysubsection{Description détaillée}
Fichier d\textquotesingle{}en-\/tête de la classe \mbox{\hyperlink{class_ecran}{Ecran}}. Cette classe est utilisée afin de communique en UART avec l\textquotesingle{}écran sur la Raspberry\+Pi. 

\begin{DoxyAuthor}{Auteur}
Samuel-\/\+Charles DITTE-\/\+DESTREE (\href{mailto:samueldittedestree@protonmail.com}{\texttt{ samueldittedestree@protonmail.\+com}}) 
\end{DoxyAuthor}
\begin{DoxyVersion}{Version}
1.\+0 
\end{DoxyVersion}
\begin{DoxyDate}{Date}
31/05/2022 
\end{DoxyDate}

Définition dans le fichier \mbox{\hyperlink{ecranlib_8h_source}{ecranlib.\+h}}.

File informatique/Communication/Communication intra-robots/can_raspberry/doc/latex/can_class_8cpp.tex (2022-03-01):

\hypertarget{can_class_8cpp}{}\doxysection{Référence du fichier can\+Class.\+cpp}
\label{can_class_8cpp}\index{canClass.cpp@{canClass.cpp}}
{\ttfamily \#include $<$stdio.\+h$>$}\newline
{\ttfamily \#include $<$stdlib.\+h$>$}\newline
{\ttfamily \#include $<$string.\+h$>$}\newline
{\ttfamily \#include $<$unistd.\+h$>$}\newline
{\ttfamily \#include $<$iostream$>$}\newline
{\ttfamily \#include $<$net/if.\+h$>$}\newline
{\ttfamily \#include $<$sys/ioctl.\+h$>$}\newline
{\ttfamily \#include $<$sys/socket.\+h$>$}\newline
{\ttfamily \#include $<$linux/can.\+h$>$}\newline
{\ttfamily \#include $<$linux/can/raw.\+h$>$}\newline
{\ttfamily \#include $<$thread$>$}\newline
{\ttfamily \#include \char`\"{}can\+Class.\+h\char`\"{}}\newline
{\ttfamily \#include \char`\"{}define\+Can.\+h\char`\"{}}\newline

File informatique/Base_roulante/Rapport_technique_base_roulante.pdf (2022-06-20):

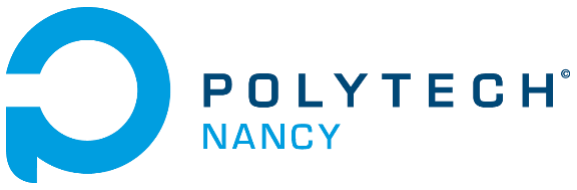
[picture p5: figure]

Juin 2022

# Coupe de France de Robotique

# Base roulante

## Lucie GARNIER

### Tuteur : M. NOIZETTE

# Sommaire

Figure 1 : Schéma du montage pour piloter un moteur | 4
Figure 2 : Principe de fonctionnement d’un timer | 5
Figure 3 : Capture d’écran du logiciel STM32, pour configurer le timer 1 | 7
Figure 4 : Capture d’écran du logiciel STM32, pour activer les interruptions du timer 1 | 7
Figure 5 : Capture d’écran du logiciel STM32, pour paramétrer le DMA du timer 1 | 8
Figure 6 : Pinout du driver TMC2208 | 9
Figure 7 : Schéma des pins utilisé sur la STM pour élaborer la carte moteur | 9
Figure 8 : Schéma des différentes directions et rotations de la base roulante | 11
Figure 9 : Signaux du timer et des trois moteurs | 12
Figure 10 : Fréquence généré par le timer maître du contrôle moteur d’une accélération | 13
Figure 11 : Schéma d’une direction alternative | 15
Tableau 1 : Paramétrage du timer 1 pour la base roulante | 6
Tableau 2 : Paramétrage desmicro-steps | 9
Tableau 3 : Trame déplacement | 10
Tableau 4 : Trame moteur | 11

## I - Introduction

L’objectif de ce pôle base roulante est de réaliser la partie informatique qui permettra au robot de se déplacer. Nous avons recommencé depuis le début toute la partie base roulante, l’objectif est d’avoir une base fiable en fin d’année et de l’améliorer au fil des ans.

Cette année, nous avons choisi de réaliser une base roulante avec trois roues, contre quatre l’année précédente. Cette solution nous permet de ne pas avoir de problèmes d’hyperstaticité. Nous utilisons des roues holonomes, ce sont des roues omnidirectionnelles. Leur principal avantage est que nous pouvons aller dans six directions différentes sans effectuer de rotations, ce qui est un gain de temps et d’énergie. Chaque roue est motorisée par un moteur NEMA 17, lui-même piloté par un driver TMC2208. On gère les pilotes des moteurs avec un microcontrôleur STM32 (modèle de carte nucléo L432KCU3). Ce microcontrôleur est commandé par la stratégie, qui envoie les actions que la base roulante doit effectuer via le bus CAN.

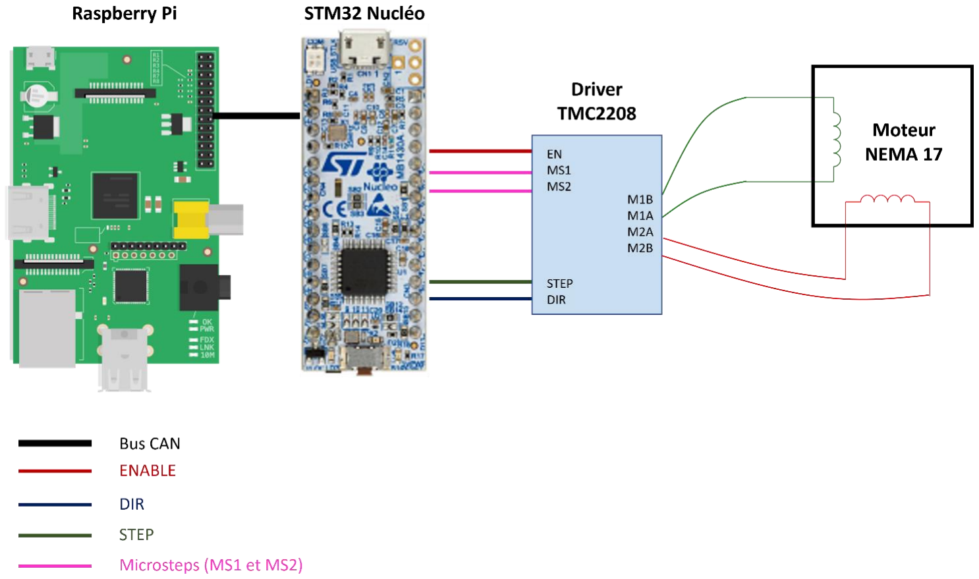
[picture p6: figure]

Figure 1 : Schéma du montage pour piloter un moteur

## II - Configuration de STM

## II.a. - Timers

Pour programmer les timers, il faut ouvrir le fichier IOC et sélectionner timer dans la colonne de gauche. L’Autoreload Regiter (ARR) est commun à toutes les channels du timer, alors que le Capture/Compare Register (CCR) est spécifique à chaque à channel. L’ARR va définir la période à laquelle l’interruption va avoir lieu, tandis que le CCR définira la largeur de l’impulsion. Nous avons ensuite deux modes : haut ou bas. Sur la Figure 2, c’est le mode haut qui est représenté, le mode bas est son complémentaire. Chaque channel de timer est reliée à une unique pin, en revanche une pin peut être connectée à plusieurs channel de différents timers.

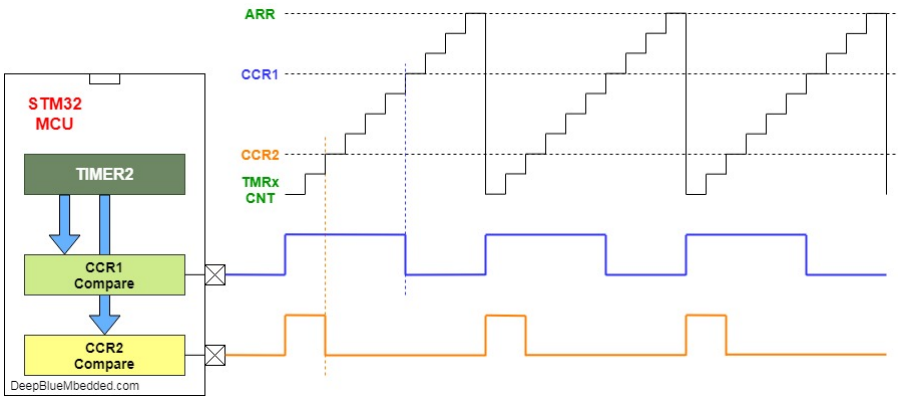
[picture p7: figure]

On commence par sélectionner le timer souhaité et on active une horloge (clock source). On utilise l’horloge interne mais on pourrait aussi utiliser une horloge externe. Cependant, toutes les cartes ne dispose pas de cette source externe il faut donc s’assurer qu’elle est bien présente. Puis, on choisit le mode de fonctionnement du channel, dans notre cas on choisit PWM Generation Channel 1. Ce mode nous permet d’avoir un signal de sortie sur la pin PA8, ce qui est pratique pour le débogage. Ensuite, il faut paramétrer le timer, dans configuration et parameter settings :

- Prescaler : permet de diviser la fréquence source. Il faut soustraire 1 pour que la sortie soit bien à la valeur souhaitée, sinon il y aura un léger décalage.

fréquence de sortie prescaler =

fréquence clock
prescaler
- Counter mode : en mode up commence à compter à partir de 0 et incrémente. A l’inverse, down va partir de la valeur de l’ARR et décrémenter jusqu’à 0. Il existe un troisième mode, center align, celui-ci va démarrer à 0, incrémenter jusqu’à l’ARR au lieu de recommencer à 0 comme le mode up, il va décrémenter jusqu’à 0.
- Counter period (AutoReload Register) : c’est l’ARR, il faut soustraire 1, car le compteur commence à 0 et non à 1, sans la soustraction, on aurait une fréquence qui ne serait pas tout à fait celle que l’on souhaite. On lui donnera une valeur de départ pas très grande pour

Figure 2 : Principe de fonctionnement d’un timer éviter qu’il ne mette sa valeur maximum par défaut et que la première interruption ait lieu après une longue attente. Cependant, cette valeur sera changée par la suite lors des phases d’accélérations et de décélérations, puisque c’est ce qui nous permet de changer de vitesse.

fréquence de sortie ARR =

fréquence de sortie prescaler ARR
- Pulse : c’est le CCR, la durée du temps haut, il doit toujours être inférieur à l’ARR. Ici, on lui donnera une valeur fixe, car on joue sur la durée de la période et non la largeur de l’impulsion pour définir la vitesse.

Nous laisserons les autres paramètres avec leur valeur par défaut.

Il faut faire attention aux nombres de bits sur lequel les nombres sont codés. Ici, on a des valeurs faibles, mais si on venait à avoir besoin de nombre plus grands, il faudrait choisir le timer en conséquence. Par exemple, nous utilisons timer 1, dont l’ARR est codé sur 16 bits, alors que celui du timer 2 est sur 32 bits. Certains timers, sur la carte n’ont qu’une seule channel, si on venait à avoir besoin plusieurs channel et qu’elles devaient être sur le même timer, c’est un élément qu’il faudrait aussi prendre en compte.

Parameter Setting | Valeur
Timer | TIM1
Clock Source | Internal clock
Channel 1 | PWM Generation CH1
Prescaler | 16-1
Counter mode | Up
Counter Period (Autoreload Register) | 100-1
Pulse | 1
Tableau 1 : Paramétrage du timer 1 pour la base roulante

Calcul de la fréquence obtenue :

fréquence de sortie prescaler =

fréquence clock
prescaler =

16 × 10⁶
16 = 1MHz

fréquence de sortie ARR =

fréquence de sortie prescaler
ARR | =

1 × 10⁶
100 = 10 000Hz

Ici, la valeur de l’ARR correspond à sa valeur lors du maintien de vitesse.

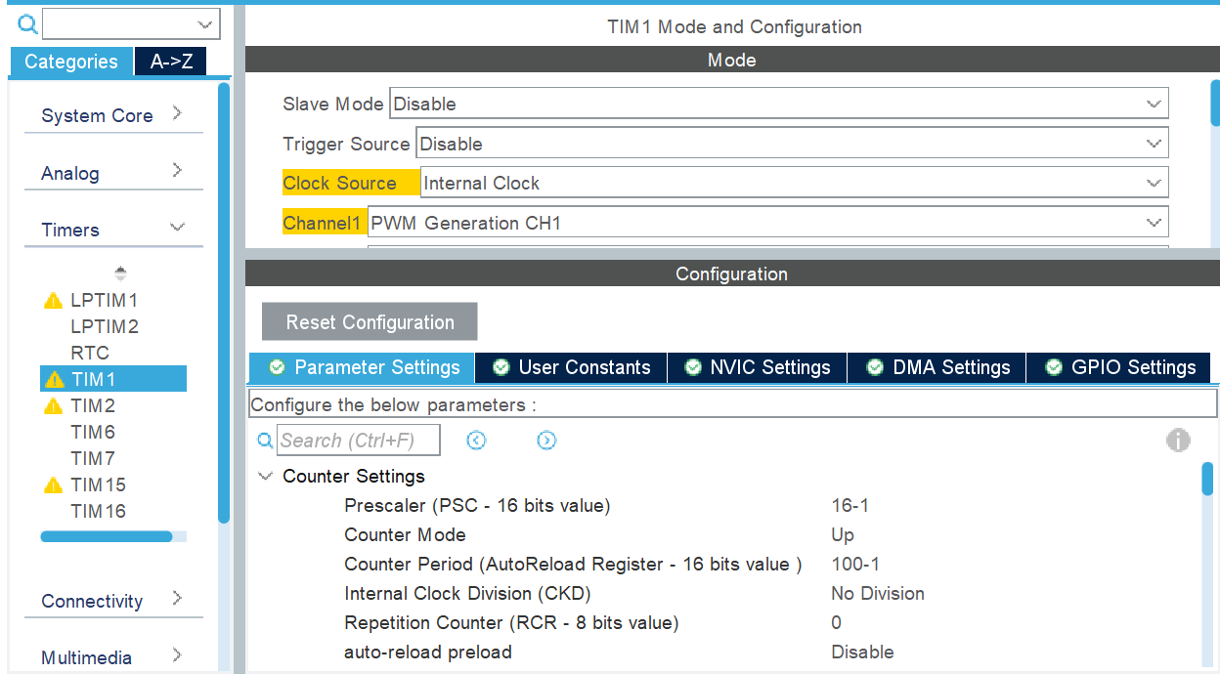
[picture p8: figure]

Cependant, même après avoir entré tous ces paramètres correctement, il ne se passera rien. En effet, il ne faut pas oublier d’activer les interruptions. Pour cela, il faut aller dans l’onglet NVIC Setting (toujours dans la configuration du timer utilisé), est cocher les différentes cases comme sur la Figure 4 ci-dessous. Sur certaines versions, il est possible de n’avoir qu’une seule case à cocher et qui activera toutes les interruptions.

Figure 3 : Capture d’écran du logiciel STM32, pour configurer le timer 1

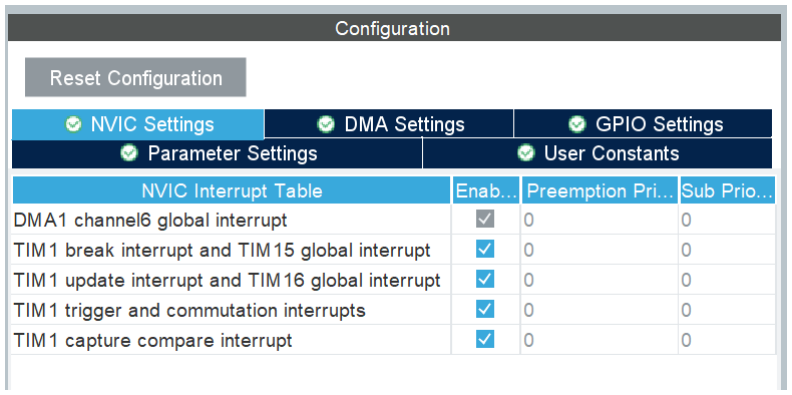
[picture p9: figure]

Figure 4 : Capture d’écran du logiciel STM32, pour activer les interruptions du timer 1

### II.b. - Direct Memory Access (DMA)

L’Accès direct à la mémoire est un procédé qui permet à des données de circuler depuis, ou vers, un périphérique et d’être transférées vers la mémoire principale, grâce à un contrôleur adapté et avec une intervention minime du microprocesseur (pour commencer et terminer l’opération). Ce qui permet au microprocesseur d’effectuer d’autres actions pendant le processus.

Nous allons utiliser ce procédé pour charger les tableaux d’accélérations et de décélérations (la génération de ces tableaux sera vu dans une prochaine partie). Pour cela, toujours dans la partie configuration du timer, on va dans l’onglet DMA. Par défaut aucun DMA n’est actif, nous allons donc en ajouter un avec add. On va ensuite le paramétrer :

- DMA request : on sélectionne l’option avec up
- Direction : nous avons deux options memory to peripheral (on envoie des données vers un périphérique) ou peripheral to memory (on récupère les données d’un périphérique et on les envoie à la mémoire). Nous choisissons la première option.

Ensuite dans DMA request settings :

- Mode : nous avons le choix entre circular, dans le cas d’un tableau les cases de ce dernier seront envoyées une à une, et lorsqu’on arrivera à la fin du tableau on recommencera à renvoyer les données à partir de la première case du tableau. Alors qu’avec le mode normal, la première fois que l’on arrive à la fin du tableau, on garde la dernière valeur envoyée, on ne recommence pas. C’est cette deuxième option que nous choisissons.
- Increment address : peripheral ou memory, nous cochons memory, car c’est l’adresse du tableau qui se trouve dans la mémoire que nous voulons incrémenter.
- Data width : on transmet un word à chaque fois.

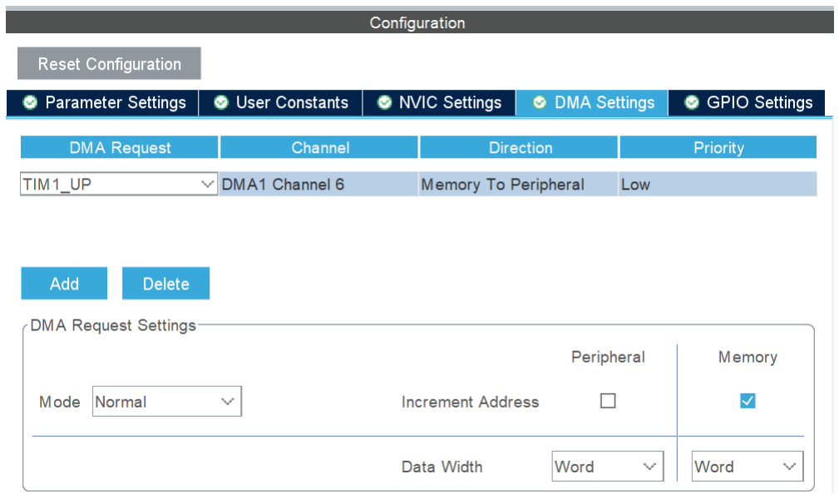
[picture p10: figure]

Figure 5 : Capture d’écran du logiciel STM32, pour paramétrer le DMA du timer 1

## III - Gestion des moteurs

### III.a. - Electronique des moteurs

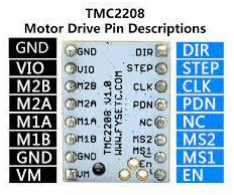
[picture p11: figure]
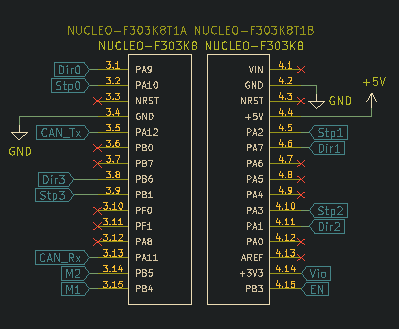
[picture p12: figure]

Tout d’abord, nous configurons la taille des pas. Avec la nouvelle version de la carte moteur, le paramétrage de la taille des pas se fait maintenant informatiquement, alors qu’avec l’ancienne carte cela dépendait d’une combinaison d’interrupteurs.

Sans diviseur, il faut deux cents pas pour faire un tour complet. Dans l’IOC, ces pins sont en mode Push Pull. Ci-dessous, le Tableau 2 indique le paramétrage des pins pour obtenir la taille de pas souhaitée. Nous choisissons de configurer les drivers avec des demi-steps. Pour cela, nous utilisons la fonction motor_micro_step(), qui prend en entrée l’état des pin MS1 et MS2, et définit la même taille de pas pour tous les moteurs.

MS1 | MS2 | Diviseur des micro-steps
GND | GND | 8
VCC_IO | GND | 2
GND | VCC_IO | 4
VCC_IO | VCC_IO | 16
Tableau 2 : Paramétrage des micro-steps

Figure 7 : Schéma des pins utilisé sur la STM pour élaborer la carte moteur

Figure 6 : Pinout du driver TMC2208

Pour que les moteurs puissent tourner, il faut qu’on courant électrique passe dans les bobines. Cela est permit avec la pin enable, qui est en mode Push Pull. Comme les micro-steps, sur la carte précédente, enable était activé, ou non, grâce à un interrupteur. La fonction motor_en(), permet d’activer ou de désactiver tous les moteurs en même temps. Si la fonction a pour paramètre SET, les moteurs ne sont pas actifs, au contraire si le paramètre est RESET alors les moteurs sont actifs. Lorsque les moteurs sont actifs et à l’arrêt ils sont clampés, c’est-à-dire qu’il faut forcer pour leur faire passer un pas.

Le sens de rotation du moteur dépend de l’état de la pin dir, qui est aussi en mode Push Pull. Nous commandons la direction d’une unique roue avec la fonction motor_dir(). Dans la configuration actuelle, c’est-à-dire lorsque le fil noir est branché sur A1, et lorsque la pin est à l’état haut, le moteur tourne dans le sens trigonométrique, à l’inverse, lorsqu’elle est à l’état bas, le moteur tourne dans le sens anti-trigonométrique. Cependant, si nous venions à inverser le branchement, alors le moteur tournerait dans le sens opposé. Il est donc important de toujours relier les moteurs aux drivers de la même manière.

Enfin, pour que les moteurs puissent tourner, il faut leur envoyer des impulsions, c’est la partie la plus compliquée. Nous générons des impulsions grâce au timer que nous avons à paramétré précédemment. De plus, chaque moteur possède un compteur et un diviseur qui lui sont propres et qui sont indépendants des autres moteurs. A chaque impulsion générée par le timer, cela déclenche une interruption, qui va incrémentée le compteur de tous les moteurs. Lorsqu’un compteur atteint la valeur du diviseur associé à ce même moteur, alors le moteur va effectuer un pas et le compteur se réinitialisera à zéro et recommencera à s’incrémenter dès la prochaine interruption.

### III.b. - Gestion des déplacements

La base roulante fonctionne avec des unités qui sont trop abstraites pour qu’une personne ou un autre système puissent les interpréter. C’est pour cela qu’il faut convertir les unités du système international en unités de la base roulante. Nous réalisons ces calculs, sur la Raspberry Pi, grâce à une fonction qui va convertir une « trame déplacement », telle que sur le Tableau 3, en une « trame moteur », telle que sur le Tableau 4.

On donne en entrée de la fonction une trame déplacement, qui est composée de trois valeurs :

- Vitesse : en millimètre par seconde, ce qui nous permet de toujours donner un nombre entier et de ne pas avoir de nombre à virgule ce qui serait plus compliquer à gérer.
- Distance : en millimètre, comme précédemment nous donnons toujours un nombre entier.
- Direction : est un nombre entre 1 et 8. Si le nombre est compris entre 1 et 6, le robot avancera dans l’une des directions comme indiquée sur la Figure 8. Si l’on donne 7 ou 8 en argument le robot effectuera une rotation sur lui-même.
Nombre de bits | 16 | 16 | 8

Description

Vitesse

[mm/s]

Distance

[mm]

Direction

Tableau 3 : Trame déplacement Trame à convertir, envoyée par la stratégie

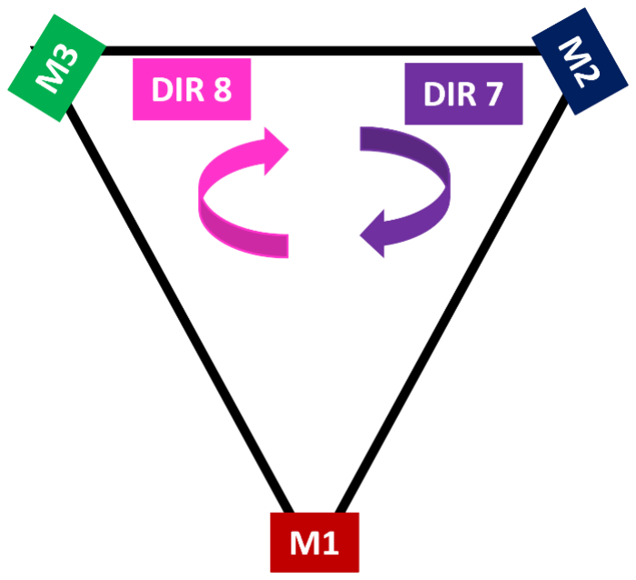
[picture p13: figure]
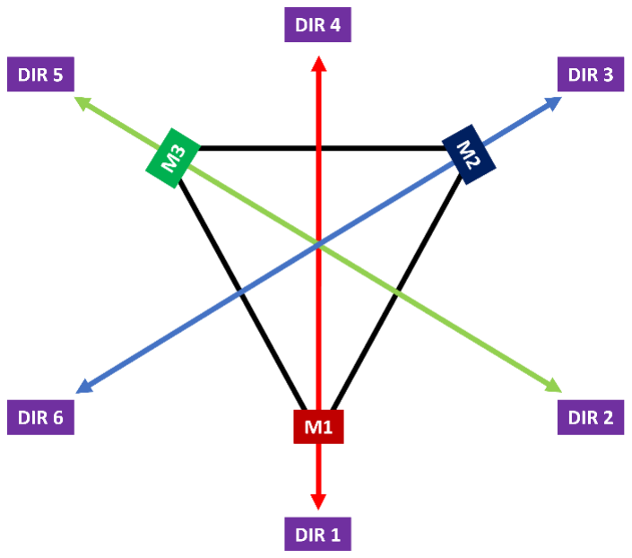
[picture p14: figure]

La fonction de conversion retourne une trame moteur, cette dernière est composée de sept valeurs :

- Nombre de steps : c’est le nombre de pas que le robot devra effectuer, le nombre d’impulsions qui seront émises par le timer.
- Trois diviseurs (un pour chaque moteur) : c’est ce qui permet de gérer la vitesse. Plus le diviseur est grand moins le robot va vite.
- Trois directions (une pour chaque moteurs) : c’est un booléen qui indique dans quel sens la roue va tourner. Par exemple, si le robot tourne sur lui-même les trois roues tourneront dans le même sens. Alors que si le robot effectue une ligne droite, il y aura une roue à l’arrêt, une roue qui tourne dans un sens et la dernière roue qui tournera dans le sens opposé à la deuxième.
Nombre de bits | 32 | 8 | 8 | 8 | 1 | 1 | 1
Description | Nombre de steps | Diviseur moteur 1 | Diviseur moteur 2 | Diviseur moteur 3 | Direction moteur 1 | Direction moteur 2 | Direction moteur 3

Tableau 4 : Trame moteur
Trame convertie et envoyée à la base roulante

Figure 8 : Schéma des différentes directions et rotations de la base roulante

### III.c. - Gestion de la vitesse et des accélérations, décélérations

Pour gérer la vitesse, on change la valeur de la période entre deux impulsions, c’est-à-dire on change l’ARR. Cependant, nous avons un unique timer pour trois roues et nous voulons qu’elles puissent avoir des vitesses différentes. Pour cela on ajoute deux variables, un « compteur » et un « diviseur », pour chaque moteur. Le principe est simple, le timer émet des impulsions, à chaque impulsion, le compteur de chaque moteur s’incrémente de 1. Lorsque qu’un compteur atteint la valeur du diviseur de son moteur, alors il y aura une impulsion sur la pin STEP associée au moteur et il avancera d’un pas, et son compteur recommencera à s’incrémenter à partir de 0. Ainsi, plus le diviseur est grand, plus le compteur mettra du temps à l’atteindre, et donc à effectuer un pas. Pour qu’un moteur reste à l’arrêt, son diviseur doit être égal à 0. On obtient trois diviseurs différents, donc trois vitesses différentes. Sur la Figure 9, on voit que les impulsions des moteurs sont synchronisées avec celles du timer. De plus, c’est le moteur vert qui ira le plus vite et le moteur violet ira plus lentement.

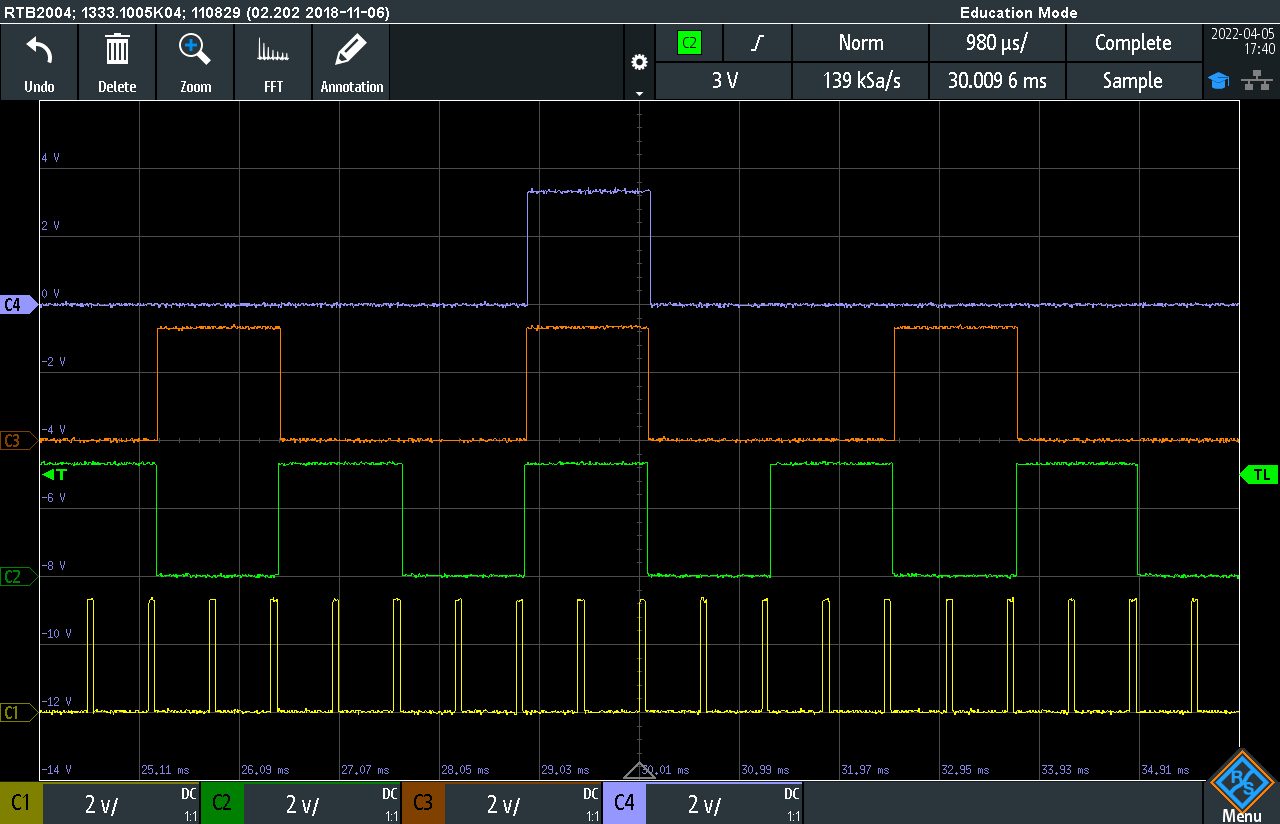
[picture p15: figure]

Figure 9 : Signaux du timer et des trois moteurs En jaune le timer, en vert le moteur 1, en orange le moteur 2 et en violet le moteur 3

Les accélérations et décélérations sont générées avec un programme à part qui ne se trouve ni sur la Raspberry Pi, ni sur la carte STM. Le programme crée un tableau, qui aura comme données toutes les valeurs d’ARR du timer, pour réaliser les accélérations en fonctions des paramètres que nous lui auront fourni précédemment, telle que la fréquence de l’horloge de la STM, le prescaler utilisé, la fréquence de départ et d’arrêt, et le temps d’accélération souhaité. Ensuite, le tableau est inversé pour avoir les décélérations. Finalement, nous récupérons la longueur des tableaux, qui est la même car les accélérations et décélérations sont symétriques, ainsi que les deux tableaux générés précédemment. On copie ces résultats et on les colle dans les fichiers utilisés pour les variables dans le code de la base roulante sur la STM. Sur la Figure 10, nous avons tracé la courbe sigmoïde de l’accélération, grâce à une fonction logistique. La fréquence de départ est de 1000Hz, et on atteint 10 000Hz en vitesse de maintien.

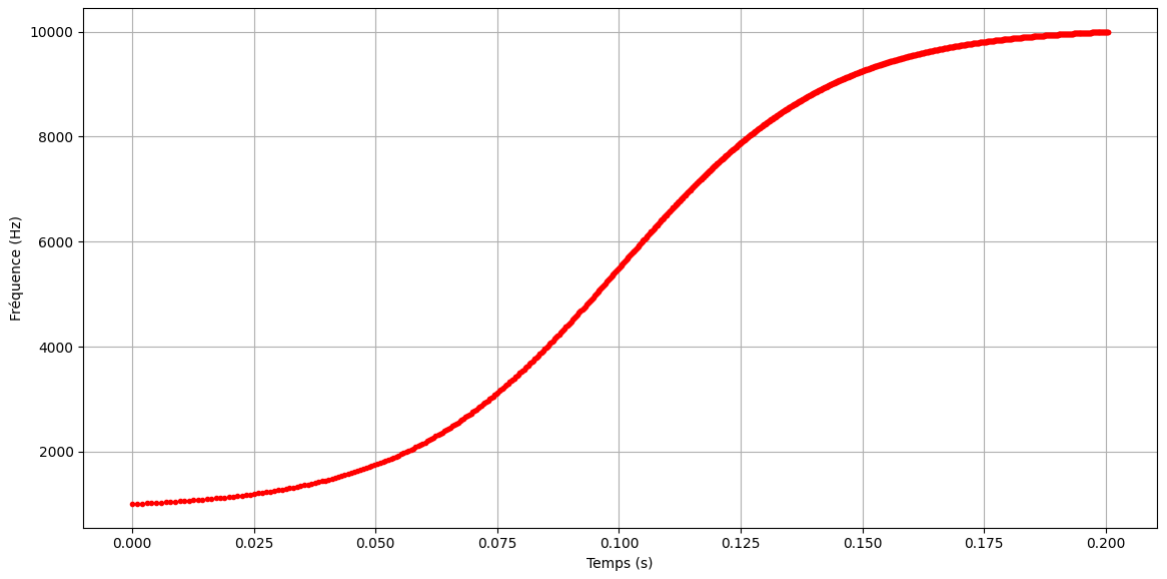
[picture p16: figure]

Figure 10 : Fréquence généré par le timer maître du contrôle moteur d’une accélération

## IV - Problèmes rencontrés

Cette année, nous avons rencontré quelques problèmes liés aux moteurs et à leur branchement. Avant de chercher les potentiels erreurs dans le programme, il faut vérifier certains points directement sur le robot. Dans un second temps, on pourra vérifier le programme.

Premièrement, nous devons nous assurer que tous les moteurs soient bien clampés lorsque que la carte de la base roulante est active. Si un des moteurs n’est pas clampé, alors le robot n’effectuera pas le bon déplacement. Par exemple, il va effectuer un cercle au lieu d’une ligne droite ou il ne bougera pas du tout si aucun moteur n’est clampé.

Deuxièmement, il faut vérifier que le branchement des moteurs est correct, que les fils n’ont pas n’ont pas été inversés, sinon cela modifiera le déplacement. Par exemple, la trajectoire sera un cercle au lieu d’une ligne droite ou lorsqu’il effectuera une rotation sur lui-même elle sera dans le sens opposé à celle que l’on souhaite.

De plus, lorsque nous avons effectué des tests en continu il s’est avéré que plus nous faisions rouler le robot moins il était précis. C’était un problème mécanique, au fil du temps, les roues se désolidarisaient du moteur, il y avait un peu de jeu et les trajectoires devinaient moins précises. Il faut donc penser à vérifier de temps en temps que toutes les pièces du robot sont bien maintenues.

Ensuite, au niveau du programme, s’il ne se passe rien, il faut vérifier que des interruptions sont bien générées. Pour cela, on regarde, avec un oscilloscope, la pin qui est associée au channel du timer que l’on a choisi précédemment, il doit y avoir des impulsions.

Lorsque nous avons eu monté le robot nous avons constaté qu’il effectuait 20% de la distance en plus lors d’un trajet en ligne droite. Cela vient de la fonction de conversion de trame déplacement en trame moteur, il doit y a avoir une erreur de calcul dans le nombre de pas mais ne l’ayant pas trouvé et étant pressés par le temps (nous avons pu effectuer ces tests seulement à la compétition), nous avons décidé d’enlever les 20% qui étaient en trop, grâce à une simple soustraction. Nous avons pu faire ceci car l’erreur était constante, elle était toujours de 20% peu importe la distance parcourue ou la direction choisie. A l’inverse lors d’une rotation sur lui-même le robot ne tournait pas assez, mais là encore l’erreur était toujours constante peu importe le sens de rotation ou l’angle choisi, nous avons donc ajouté 18,75% au nombre steps final.

Enfin, si le robot ne prend pas en compte un nouvel ordre de déplacement qui lui a été envoyé et qu’il renvoie 00, c’est qu’il est déjà en train d’effectuer un trajet. Il faut soit attendre qu’il ait fini son déplacement, soit lui ordonner de s’arrêter et renvoyer l’ordre une fois qu’il est à l’arrêt. Lorsque l’on interrompt un trajet avec le code fonction STOP, la base roulante renvoie immédiatement une trame moteur, c’est-à-dire au début de la phase de décélération, mais elle va encore parcourir une certaine distance avant d’être totalement à l’arrêt. Le nombre de pas qui est renvoyé, c’est le nombre de pas qu’il restait à effectuer pour faire complètement le trajet moins le nombre de pas qui seront nécessaire pour s’arrêter (on connaît ce nombre puisque la déclaration est toujours la même). Cependant, puisque la base roulante n’est pas à l’arrêt, si on renvoie un ordre déplacement immédiatement après la réception de la trame envoyée par la base roulante alors l’ordre ne sera pas pris en compte. Il faut attendre le temps de la décélération (temps que l’on connaît également puisque c’est toujours le même).

## V - Conclusion et perspectives

### V.a. - Gestion des accélérations, décélérations

Une des premières améliorations à apporter serait de rendre les accélérations et décélérations asymétriques. Actuellement, elles sont symétriques, ce qui pose un problème lorsque nous atteignons des vitesses élevées, de l’ordre du mètre par seconde. A cette vitesse, l’accélération se passe encore bien mais lors de la décélération le robot commence à basculer, si l’on augmentait encore la vitesse, il se renverserait complètement. En effet, le poids du robot entre en jeu, notamment celui de la batterie qui est assez important et elle est placée en hauteur ce qui augmente son impact. Il faudrait donc pouvoir rendre la décélération indépendante de l’accélération, et la rendre plus longue. Mais si nous faisons cela il faudra aussi revoir le périmètre de la détection de collision, c’est-à-dire l’agrandir car si la décélération est plus longue alors le robot parcourra une plus grande distance avant de s’arrêter.

Dans un deuxième temps, on pourra faire en sorte que les accélérations et décélérations soient calculées en temps réel. Pour cela, il faudra implémenter sur la STM le programme qui génère les tableaux d’accélérations. Cependant cela sera plus compliqué et plus long à faire que de rendre les accélérations et décélérations asymétriques.

### V.b. - Correction des déplacements en temps réel

Une autre amélioration possible est la correction en temps réel de la trajectoire avec un correcteur sur la Raspberry Pi.

Cependant, pour réaliser cela il faudra que la
base | roulante | puisse | accepter | un | nouveau
déplacement | alors | qu’elle | n’est | pas | arrêtée.
Actuellement, si le robot n’est pas totalement arrêté, il ne peut débuter un nouveau déplacement, il prendra en compte uniquement les instructions pour s’arrêter. C’est une sécurité qui a été mise en place afin d’éviter que deux instructions de trajet ne se mélangent et que le programme plante. Le robot devra aussi pouvoir changer de vitesse sans s’arrêter.

Il faudra également aller dans une direction différente des six directions possibles actuellement, comme sur la Figure 11. Pour cela, il faut que les trois roues aient une vitesse différente. Cette partie est déjà réalisée, on peut donner trois vitesses différentes mais le robot irait dans une direction qui ne serait pas
celle que l’on souhaite. Il manque les calculs qui
permettront de faire rouler le robot avec la bonne

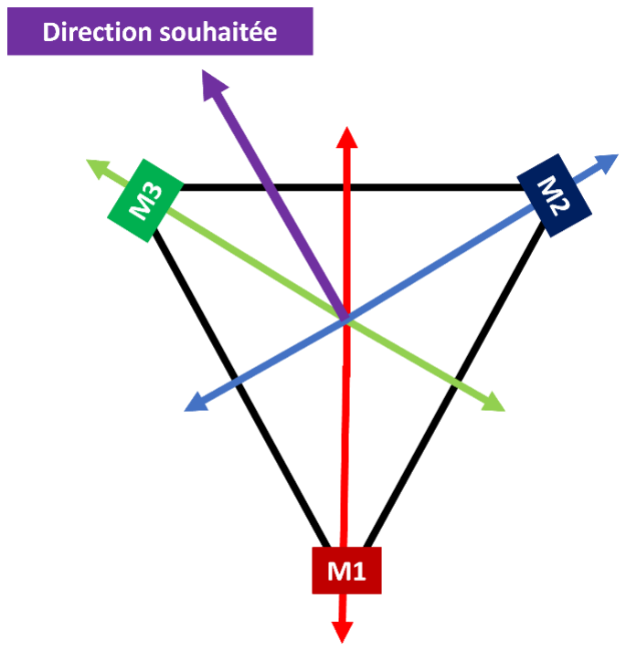
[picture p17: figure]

vitesse générale et le bon angle. | Figure 11 : Schéma d’une direction alternative

### V.c. - Conclusion

Pour conclure, cette année la base roulante a été rendue fonctionnelle et relativement fiable. Il est important de conserver ce qui as été fait et de la transmettre pour l’année suivante. En effet, la base roulante est loin d’être parfaite et nous pouvons l’améliorer de nombreuses manières.

Parmi les problèmes cités précédemment, certains étaient récurrents, mais nous perdions quand même du temps à chercher d’où le problème venait. Il faudrait en dresser une liste « problème, source du problème et solution » sur laquelle nous pourrions nous appuyer et afin de pouvoir vérifier plus facilement et plus rapidement.

Pour les années suivantes, il faudrait aussi que plusieurs personnes soient capables de comprendre le fonctionnement de la base roulante, pas forcément dans les détails mais que ces personnes puissent régler des problèmes simples et la commander.

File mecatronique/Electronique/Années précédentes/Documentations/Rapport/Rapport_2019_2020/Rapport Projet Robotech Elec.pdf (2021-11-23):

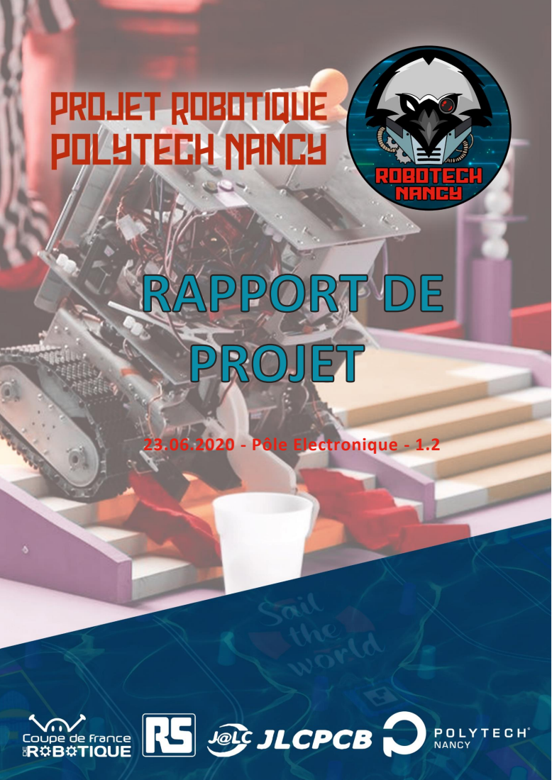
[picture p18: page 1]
23.06.2020 - Pôle Electronique - 1.2

## Page 2

23.06
P ô l e E l e c t r o n i q u e
1.2

# Révision

Version | Date | Auteur | Description
1.0 | 02/12/19 | T. BURKHARD | Création d’un modèle de rapport pour le projet
1.1 | 13/06/20 | T. BURKHARD | Changement de police de titre, adaptation des marges liées à l’entête et au pied de page
1.2 | 21/06/20 | F. SULER | Correction et syntaxe

## Page 3

# Sommaire

Table des matières

## Page 4

## Page 5

# I. Hiérarchie

Le pôle électronique est constitué de quatre étudiants : Malek AYEB, Clyde-Borel KUIATE BOGNE, Maxence THIEBAUT et François SULER.

Ce dernier est chef de pôle, responsabilité qui consiste à planifier, superviser et accompagner l’ensemble des tâches du pôle, de participer aux réunions avec les autres chefs de pôle ainsi que notre tuteur Monsieur NOIZETTE. Malgré tout, il est assujetti aux mêmes tâches que les autres étudiants.

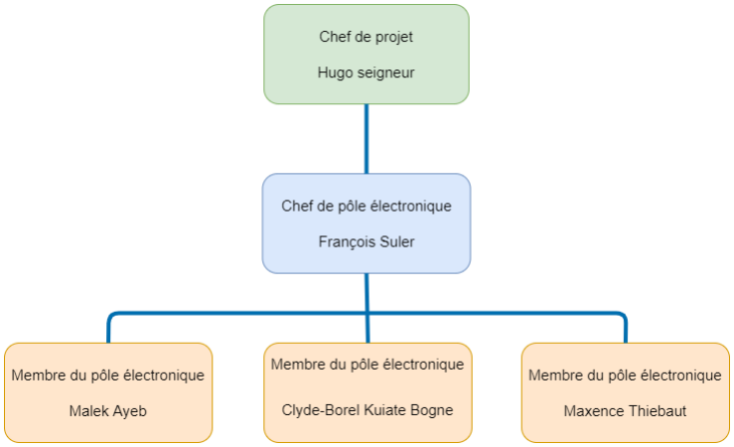
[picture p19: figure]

Figure 1: Organigramme du pôle

## Page 6

# II. Outils numériques

Pour mener à bien nos missions, nous avons eu recours à quelques logiciels, tels que Kicad, Matlab et GitHub.

## 1. Kicad

Il s’agit d’une suite logicielle de conception électronique assistée. C’est un freeware open source suffisamment performant pour effectuer la majorité des missions du pôle.

Il est composé des logiciels :

− Interface principale : Gestionnaire de projet
− Eeschema : Editeur de schéma électronique
− PcbNew : Editeur de circuit imprimé
− Gerberview : Logiciel pour visualiser des fichiers « gerber » − Cvpcb : Gestionnaire d’empreintes.

## 2. Matlab

Matlab est un logiciel de calcul matriciel développé par la société Matworks. Sa puissance de calcul fait de lui l’un des logiciels les plus utilisés dans l’enseignement et l’industrie. Il est utilisé dans plusieurs domaines, allant des mathématiques à l’ingénierie. Matlab est un logiciel propriétaire. L’Université de Lorraine possède une licence permettant à tous ses étudiants de l’utiliser gratuitement au cours de leur scolarité.

## 3. Github

GitHub est un service web d’hébergement de développement collaboratif maintenu par Microsoft. Il est basé sur le logiciel de gestion de version Git. Il propose des services gratuits et payants.

Dans le cadre de notre projet, nous avons utilisé l’application GitHub desktop. Ce service nous a servi comme site de dépôt de nos travaux.

## 4. Kanboard

Kanboard est un logiciel de planification et de suivi de projet. Il est basé sur la méthode Kanban adaptée à notre philosophie de gestion. Il nous permet de suivre les tâches en cours, terminées, prêtes à être commencées ou en attente. De plus il dispose d’un outil de planification et de gestion du temps d’exécution. Cela nous permet de faire un lien entre planification et réel.

## Page 7

# III. Architecture du robot

L’architecture de robot est un sujet central dans un projet de cette complexité. En effet, celle-ci va être critique dans nos décisions.

Plusieurs choix s’offraient à nous :

− Une centralisation totale

Elle est caractérisée par le fait que nous avons uniquement une Raspberry Pi. Elle contrôle l’ensemble des actionneurs via des drivers dédiés et ses ports GPIO, bus UART, SPI…

Cette méthode certes complexe au niveau matériel, demandant également des efforts importants de développement soft, réduit toutefois drastiquement le nombre de composants dans le robot avec pour désavantage un coût importantsur le plan du dépannage et débogage.

− Un binôme RPi-STM32H7

Le STM32H7 est la famille la plus puissante de microcontrôleurs STM32. Ces microcontrôleurs sont capables de satisfaire l’ensemble des besoins hardware du robot. L’un de ses désavantages, la parallélisation des tâches complexifiée.

− Une indépendance des modules

Cette méthode a pour but de rendre chaque partie du robot indépendante. Chaque carte intègre un microcontrôleur STM32F1 avec un soft spécifique et un protocole de communication défini.

Cette méthode permet de réduire l’effort sur le développement soft et améliorer la maintenabilité du robot. Il est également possible de tester facilement chaque carte, de manière indépendante,sur un banc de test unique et de ne remplacer que les problématiques, réduisant ainsi le temps d’intervention, en cas de maintenance.

Nous nous sommes ainsi orientés vers une architecture décentralisée. Le microcontrôleur de prédilection est le STM32F103C8T6, pour des raisons de disponibilité des interfaces, d’organes internes (nombre de timer, interfaces CAN SPI I2C…) et de fabrication. Son boitier TQFP est facilement soudable à la main et sa disponibilité comme composant basique au service SMT Assembly du fabricant JLC PCB, est un réel avantage.

Nous avons également fait le choix d’une communication via un bus CAN unique pour des questions de résilience électromagnétique, d’adressage, d’absence de maître et de simplicité d’implémentation au niveau matériel.

Vous pouvez voir sur la figure 2 que nous avons choisi de multiplier les cartes indépendantes.

## Page 8

Elle représente l’ensemble des interconnections entre organes du robot.

Dans un premier temps, nous avons une communication entre l’ensemble des cartes sur un unique réseau monté sur un bus CAN.

Dans un second temps, nous avons une carte d’alimentation qui distribue la puissance aux différentes cartes. Sur cette dernière nous avons trois organes de mesure de puissance :

− Un premier permet de mesurer la puissance soutirée pour le groupe de motorisation.
− Un second mesure la puissance soutirée par le bus 12V.
− Un troisième permet de connaître la puissance consommée par le bus 5V. (La consommation de la RPi étant connue directement par cette dernière)

Nous avons également fait le choix de permettre la coupure des deux rails de puissance, à savoir : le rail de tension batterie correspondant à la puissance envoyée aux moteurs, et le rail 12V, qui correspond à la puissance envoyée aux différents accessoires.

Cette coupure peut être effectuée de deux manières : via le microcontrôleur par ses GPIO (coupure sélective d’un rail ou l’autre) ou, coupure des deux rails avec le bouton d’arrêt d’urgence. Ce dernier ne coupera que la puissance des accessoires et des moteurs.

Ce choix a été fait dans le but de maintenir l’alimentation des parties décisionnelles du robot (RPi, STM, capteurs), pour nous permettre de garder des informations nous permettant ensuite, de comprendre la défaillance qui a conduit à l’arrêt d’urgence.

## Page 9

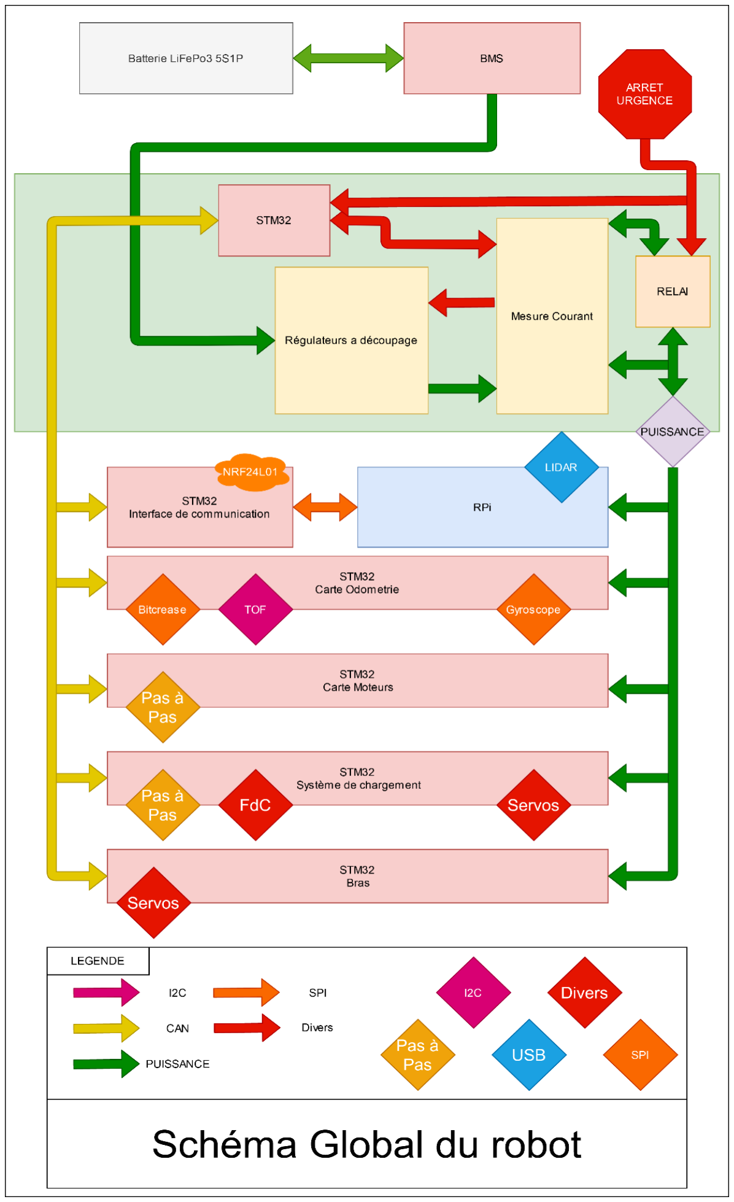
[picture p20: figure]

Figure 2: Schéma d'architecture du robot

## Page 10

# IV. Historique pour chaque partie

## 1. Les connecteurs

Le choix des connecteurs est essentiel. Nous avons pu apprendre des années passées, que ces derniers sont garants de la sécurité des connexions, un mauvais choix pouvant faire la différence entre un robot fonctionnel et un robot inutilisable à la suite d’une mauvaise connexion. Le choix a donc été fait d’investir dans des connecteurs MOLEX à détrompeurs et verrouillage.

Chaque type de connexion à son connecteur spécifique évitant ainsi, par exemple, de connecter un rail de puissance 5V avec un autre de 12V ou alors de connecter le bus CAN à la sortie VBAT

Les choix ont donc été les suivants :

Bus | Type | contacts | schéma
Entrée batterie | Micro-fit | 02x02
Sortie 5V | Nano-fit | 01x02
Sortie 12V/5V | Nano-fit | 01x03
Sortie Moteurs | Micro-fit | 02x03
BUS CAN | SL | 01x02
Prog/Debug | Nappe | 02x10 | Voir librairie Kicad

Pour ce qui est des connecteurs en sortie de carte, ils sont à adapter à la cible mais, doivent être différents de ceux cités ci-dessus.

## 2. Les capteurs d’odométrie absolue

Notre robot doit se déplacer en autonomie. Pour ce faire il doit avoir la capacité décisionnelle de contrôler ses actions. Il est donc nécessaire qu’il soit équipé des capteurs pour en temps réel déterminer sa position, son déplacement ainsi que son environnement.

## Page 11

## a. Recherche des capteurs

Dans le choix du capteur nous avons élaboré une « matrice de choix » comparant les différents capteurs disponibles selon des critères en adéquation avec le projet.

Critères

Technologies | Ultrason | Infrarouge | Laser
Références | HC - SR04 | GP2Y0A710K0 F | GP2Y0A2 1 | VL53L0X | TF Mini | YLIDAR X2
Plage de mesures | 2cm-400cm | 100 to 550 cm | 10 cm à 80 cm | 10cm-120 cm | 0.3m-12m | 0.10-8m
Précision | 3mm | 3mm | 3mm | 3mm | 1% (less than 6m), 2% (6m-12m) | 0,02
Communication | - | - | - | I2C interface | UART /RX/TX | USB
Courant nominal | 15 mA | 30 mA | 30 mA | 19mA | - | 350 mA
Tension d'alimentation | 5V | 5V | 4,5V à 5V | 2,6-3,5V | 4.5V-6V | 4.8V~5.2V
Angle faisceau sortant / Longueur d'onde | 15° | λ = 870 ± 70nm | - | 25°,35° | 2.3° | -
Fréquence de balayage | - | - | - | - | - | 5 à 8 Hz
Prix | 4,12 € | 7 € | 10,50 € | 2,26€ | 40 € | 72 €
Utilisation | Facile | Facile | Facile | Facile | Facile | Difficile
Points pondérés | 1,5 | 3 | 2 | 3 | 5 | 4
Rang | 5 | 3 | 4 | 3 | 1 | 2

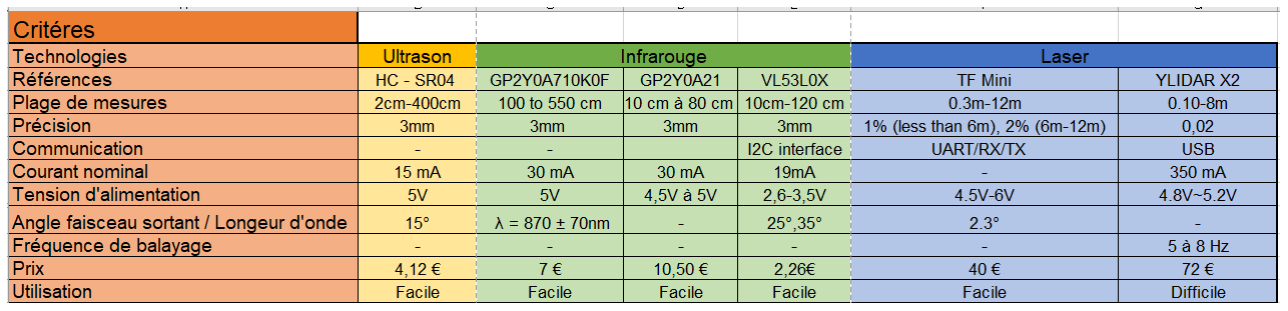
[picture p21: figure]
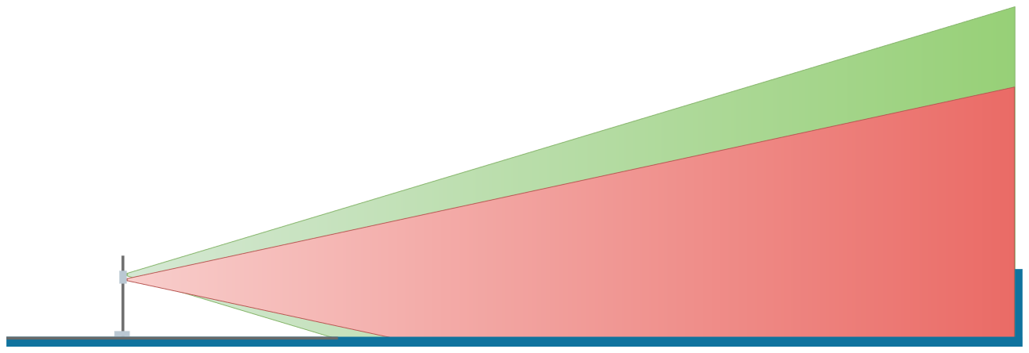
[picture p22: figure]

## Page 12

Figure 3: la matrice de choix des capteurs de distance

## b. Banc d’essai des capteurs ToF

Afin de caractériser les capteurs ToF (Time of Flight), nous avons créé un banc d’essai qui nous a permis d’effectuer des séries mesures, avec précision. La partie physique du banc d’essai a été réalisée par le pôle Conception et Fabrication.

Il est constitué de deux réglets, le premier, horizontal, pour faire évoluer la distance à la cible et le second, vertical, pour faire évoluer la distance entre le capteur et le plateau de jeu.

Un capteur ToF produit une lumière par le biais de son émetteur. Elle est réfléchie sur les objets présents dans le faisceau. Une partie de cette dernière est alors renvoyée vers le capteur qui peut alors la détecter. On mesure alors le delta de temps entre l’émission et la réception d’une impulsion. De cette durée, on peut en déduire la distance.

On peut caractériser un capteur par l’angle d’ouverture du cône de détection. Les capteurs ultra-sons ou à LED infrarouge auront un grand angle de détection, contrairement aux technologies laser caractérisées par un rayon faiblement dispersé.

Figure 4: schéma de notre banc d’essai

## Page 13

Le premier capteur ToF que nous avons étudié était le VL53L0X. Fabriqué par ST MICRO, il utilise une technologie infrarouge. Nous avons observé qu’à partir d’une certaine distance, la plupart des rayons lumineux n’atteignent pas la bordure de l’aire de jeu (figure 4), raison pour laquelle nous avons développé une procédure de caractérisation pour définir l’intervalle dans lequel le capteur a des performances acceptables.

Le même outil a été mis en œuvre pour caractériser le TF Mini de la marque BENEWAKE.

## c. Caractérisations des capteurs ToF

Une réponse d’un capteur peut principalement être caractérisée par deux erreurs, l’erreur systématique et la dispersion. Le but de la caractérisation est d’estimer ces deux valeurs.

Une erreur systématique est compensable en appliquant une correction à la valeur renvoyée par le capteur. La dispersion, quant à elle, peut être réduite en filtrant les données. Par exemple sur une série de données, on peut retirer les valeurs aberrantes et utiliser un filtre moyen pour en déduire la valeur la plus pertinente. Il est possible d’apporter, si nécessaire, à cette valeur, une correction mathématique, pour compenser l’erreur systématique.

L’analyse des données récoltées a pour objectif de définir le profil de la correction à appliquer pour nos capteurs.

Ce traitement a été automatisé grâce à un programme sur MatLab. Il a pour fonction de trier les données et dessiner la fonction de répartition pour chaque distance (figure 5).

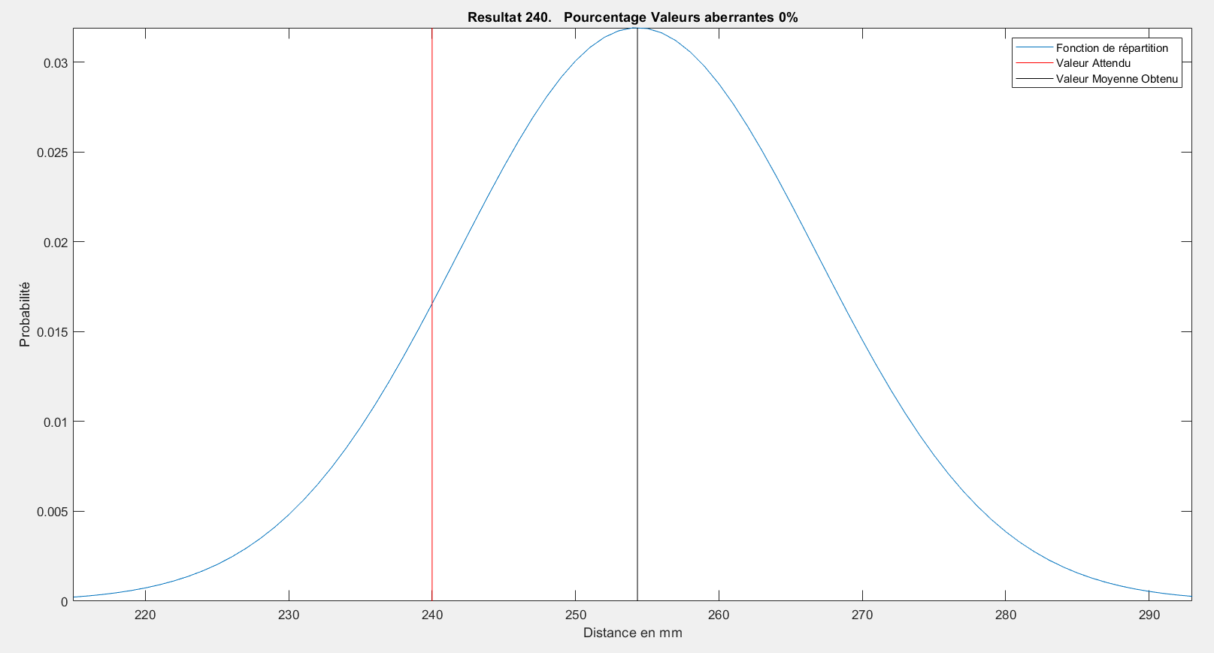
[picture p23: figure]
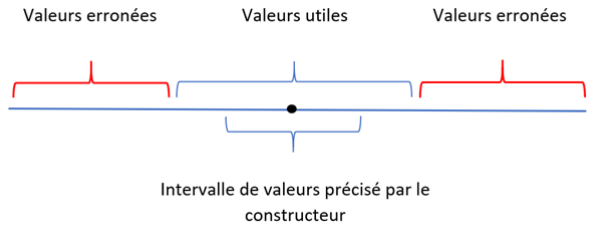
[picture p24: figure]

## Page 14

Figure 5: Distribution des données

Les données suivent une distribution normale. L’écart-type augmente avec la distance et varie en fonction du modèle de capteurs. Cette valeur est à prendre en compte pour le choix d’un capteur.

On calcule également l’écart entre la valeur attendue et la valeur moyenne des données ainsi que le taux de valeurs aberrantes (figure 6).

L’erreur ainsi caractérisée s’avère supérieure à celle donnée par le constructeur.

Ce traitement est effectué pour de multiples distances, avant d’appliquer les calculs pour la caractérisation.

Figure 6: intervalle de distribution des valeurs


## Page 15

Afin de proposer un étalonnage des capteurs, nous déterminons un modèle mathématique qui compensera l’erreur systématique.

Des capteurs ont besoin de cet étalonnage pour être fiables. Nous appliquons une régression polynomiale pour déterminer les paramètres du modèle de correction (figure 7).

Figure 7: Détermination de la courbe de correction

## 3. La base roulante de test

Nous avons fait le choix de réaliser une première base roulante de tests permettant au pôle informatique d’avoir un support pour affiner le modèle de déplacement, de communication etc…

Nous avons réalisé une base roulante sur une breadboard, permettant des modifications simples du câblage.

Pour cette partie nous avons utilisé :

− 4 drivers de moteurs pas à pas TMC2208 − 1 nucleo STM32 format Arduino nano − 1 level shifter 8 voies
− 1 batterie LiPo 3S
− 4 Moteurs pas à pas NEMA17

## Page 16

## 4. L’alimentation

## a. Les cellules

Du fait de fortes contraintes de volume, de caractéristiques électriques et de sécurité, notre choix s’est porté sur la technologie Lithium – Fer – Phosphate (LiFePO4 ou LFP).

Cette technologie dispose d’une énergie volumique intéressante (190 à 240 Wh/L), le double des batteries au plomb. En outre, elle dispose d’une puissance de pointe de près de 3 fois celle des technologies n’utilisant pas de lithium.

Les technologies lithium ne sont pas sans risque. Un mauvais entretien, une sous-tension, une surtension ou un courant appelé trop fort peut endommager la batterie et dans bon nombre de cas entrainer un gonflement qui peut être suivi d’un dégagement gazeux, voire d’un incendie. Pour cette raison, le règlement impose aux batteries type Li-Po ou Li-ion d’être stockées dans des sacs ignifugés. La technologie LiFePO4 que nous utilisons n’est pas aussi contraignante et nous dispense règlementairement d’un tel dispositif.

Nous avons donc fait ce choix pour nous permettre de réaliser nos propres batteries, pour gagner en expérience, en flexibilité, en maintenabilité et en place.

## b. Le BMS

La carte BMS (Battery Management System) est indispensable pour la sécurité de notre alimentation. Elle nous assure une protection contre les courts circuits, les surcharges, les décharges et les surintensités.

Pour une question de simplicité et de gain de temps, nous avons préféré commander une carte.


Figure 8: photo du BMS choisi

## Page 17

On notera que ce dispositif n’est présent uniquement que pour protéger la batterie et non le robot.

## c. Les tensions de cellules

Afin de pouvoir visualiser le niveau de batterie et l’état de chaque cellule nous avons conçu une carte qui calcule la différence entre cellules par un soustracteur (montage AOP soustracteur).

En ce qui concerne les résistances on sait que :

On veut que (V2-V1) soit égal à 5 Volts maximum et Vs max = 3,6 V

Donc on peut déduire la relation entre R2 et R1 :

Pour garantir une tension de 3,6 V maximum à la sortie de chaque amplificateur opérationnel, on a ajouté une diode ZENER et une résistance de 10kΩ.

## d. Carte finale

Après concertation :

− Le joulemètre, initialement prévu pour être installé sur cette carte, sera indépendant.
− Seules les mesures des tensions et des courants sur rails d’alimentation (plus de détails plus bas) seront effectuées.
− Le module de mesure de tension des cellules ne sera pas intégré à cette carte.

La carte finale aura pour rôle de produire, à partir de la tension de la batterie, les différents niveaux de tensions dont aura besoin le robot à savoir :

- VBatt-8A pour les moteurs
- 12V-2A pour les accessoires
- 5V-2A pour l’alimentation de la Raspberry Pi
- 5V-1A pour l’alimentation des différentes autres cartes


## Page 18

## 5. Système de récupération de gobelets

À la suite d’une réunion avec l’ensemble des participants du projet, nous nous sommes accordés sur un système de bras articulé et de deux ascenseurs placés de chaque côté.

## a. Les ascenseurs

Un ascenseur est composé de deux pinces dont l’une peut se déplacer sur une glissière verticale. La première étape a été de définir l’ensemble des signaux utiles pour faire fonctionner le système.

Une fois les signaux définis, nous avons pu choisir un microcontrôleur adapté. Nous avons retenu le STM32F103C8T6. Il est capable de gérer l’ensemble des signaux. Le pôle informatique l’utilise également pour d’autres applications.

Figure 9: vue 3D de la carte d'alimentation


## Page 19

Carte Ascenseur
Organe | Nom du signal | I/O STM32F103 | Type pin
P2.1 | DIR_Moteur_P-A-P_2.1 | PB2
| STEP_Moteur_P-A-P_P2.1 | PA8 | TIM1_CH1
| Fin_De_Course_P2.1 | PB14
P1.1 | PWM_Pince_P1.1 | PA0 | TIM2_CH1
PWM_Poignet_P1.1 | PA6 | TIM3_CH1
Programmation | SWCLK | PA15
| SWDIO | PA14
| NRST | NRST
| SWO | PA16
BUS CAN | CAN_RX | PA12 (TX STM) | CAN
CAN_TX | PA11 (RX STM) | CAN

Figure 10: tableau des signaux utile pour la carte d’un ascenseur

Figure 11: vue 3D de la carte d’un ascenseur

## Page 20

## b. Le bras

Carte Bras
Organe | Nom du signal | I/O STM32F103 | Type pin
Bras | RX_Bus_UART_Coude | PA2 | UART
| TX_Bus_UART_Coude | PA3 | UART
| RX_Bus_UART_Epaule | PA2 | UART
| TX_Bus_UART_Epaule | PA3 | UART
| PWM_Poignet_Bras | PA6 | TIM3_CH1
| PWM_Pince_Bras | PA0 | TIM2_CH1
| STEP_Moteur_P-A-P_Bras | PA8 | TIM1_CH1
| DIR_Moteur_P-A-P_Bras | PB2
| Fin_De_Course_Bras | PB14
Programmation | SWCLK | PA15
| SWDIO | PA14
| NRST | NRST
| SWO | PA16
BUS CAN | CAN_RX | PA12 | CAN
CAN_TX | PA11 | CAN
Figure 12: signaux utiles pour la carte d’un ascenseur

Ne connaissant pas la technologie finale des actionneurs, nous ne pouvons pas finaliser cette tâche.

## c. La programmation des ascenseurs

Les différentes étapes de la programmation des ascenseurs :

− Développement des fonctions pour les mouvements de bases
− Développement des fonctions de prise et stockage/déstockage des bouées en accord avec le GRAFCET proposé par le pôle Conception et Fabrication
− Implémentation d’une file (FIFO) pour stocker les instructions arrivant par le BUS
− Gestion de la communication sur le BUS CAN (lecture des instructions et confirmation de tâche effectuée)

La carte reçoit comme message un caractère codant l’instruction à réaliser (prise de bouées au sol ou à l’écueil, déchargement).

## 6. Le phare

La carte du phare n’étant pas dans le robot, elle n’est pas soumise aux mêmes exigences, en termes de connecteurs ou de choix des composants.

## Page 21

Au vu du cahier des charges du phare, nous nous sommes arrêtés sur le choix d’un CPLD plus adapté au besoin. Nous avons décidé d’utiliser des moteurs à courant continu, pour le déploiement du phare et pour le gyrophare qui se situe au sommet du phare.

La partie d’adaptation de la puissance envoyée aux moteurs est effectuée par un circuit intégré double pont en H : L298N.


Figure 13: vue 3D de la carte du phare

## 7. Le carte communication

La carte de communication est un organe essentiel pour le robot. En effet elle permet d’embarquer le protocole de communication sur le BUS CAN. Elle dispose également d’un moyen de communication sans fil, type Xbee ou NRF24L01. Elle permet dans le même temps d’alimenter la Raspberry. Elle respecte la norme des BOB pour Raspberry.


Figure 14: Vue 3D de la carte de communication

## Page 22

# V. Fabrication des cartes électroniques

Pour fabriquer les cartes pour le projet, nous avons deux solutions. Pour de simples prototypes ou des cartes qui doivent être prêtes rapidement, nous pouvons utiliser la fraiseuse LPKF S-100 du laboratoire d’électronique de Polytech Nancy. Si nous voulons des PCB plus professionnelles avec une couche de masque et de sérigraphie, nous pouvons passer par notre sponsor JLC PCB.

## 1. Fraiseuse LPKF S-100

La fraiseuse LPKF S-100 nous permet de créer des cartes, simples ou doubles faces. Nous pouvons raisonnablement descendre jusqu’à une largeur de piste de 0.2mm et des vias de 0.4mm de diamètre. Ces limitations ne sont pas un obstacle dans notre contexte. Elles nous permettent déjà d’utiliser une très grande majorité des composants à notre disposition. Notre principale limitation est la soudure manuelle ou au four, opération qui devient complexe avec des éléments de petites tailles comme des résistances normées 0402

La Fabrication de déroule en plusieurs étapes.

− Initialisation de la machine
− Import des fichiers « gerber »
− Placement de l’origine utilisateur sur un point de la matière première à usiner − Perçage des trous de placement
− Collage d’un film de protection sur les deux faces
− Dégagement des trous de repérages
− Marquage et perçage des trous à métalliser
− Sortie du PCB de la machine
− Remplissage des trous avec une pâte à métalliser − Retrait du surplus par aspiration
− Retrait du film de protection
− Cuisson en four à refusion
− Replacement dans la machine
− Perçage ou fraisage des trous non métallisés. − Fraisage de la première face
− Retournement la plaque
− Fraisage de la deuxième face
− Fraisage des contours
− Sortie de la carte de la machine
− Séparation du PCB du reste de la plaque
− Nettoyage avec de la paille de fer et de l’acide formique − Étamage liquide

## Page 23

Ces étapes réalisées, nous pouvons nettoyer la PCB à l’eau et une fois sèche commencer à assembler les composants

## 2. JLC PCB

JLC PCB est un fabricant industriel de PCB. Le process est sensiblement différent de la fraiseuse du laboratoire.

Au lieu d’utiliser un process abrasif, ils utilisent un process chimique tel que décrit ci-dessous :

− Import des fichiers « gerber » sur le site internet puis commande
− Vérification des règles de routage
− Assemblage avec d’autres projets pour occuper une plaque complète − Nettoyage de la plaque
− Découpe de la plaque à une dimension utilisable
− Perçage des trous à métalliser
− Nettoyage de la plaque
− Electro-plaquage (métallisation des trous à métalliser)
− Vérification de la conductivité
− Application d’une résine photosensible
− Placement d’un masque correspondant au design sur chaque face − Exposition aux UV pour polymériser la résine
− Nettoyage de la résine non polymérisée
− Dissolution du cuivre exposé
− Nettoyage de la carte
− Inspection optique
− Application d’un masque de soudure en époxy photosensible
− Séchage à 87°C
− Application d’un masque correspondant au design sur chaque face − Exposition aux UV pour polymériser le masque de soudure à garder − Nettoyage du masque non polymérisé
− Impression de la couche de sérigraphie sur les deux faces
− Finition de surface (étamage)
− Test électronique (isolation et conductivité)
− Séparation des PCB de la carte principale
− Nettoyage à ultrasons
− Inspection visuelle humaine

Une fois ces étapes réalisées il ne reste alors plus qu’à envoyer les cartes ou les amener à l’assemblage automatique.

## Page 24

## 3. SMT Assembly

L’assemblage des composants de surface est un plus non négligeable. En effet, il nous permet d’utiliser un grand nombre de composants. Certains de petite taille nous empêchent l’usage car trop difficiles à souder.

Pour nous assister nous pouvons avoir recours au service SMT Assembly mis à disposition par notre sponsor JLC PCB.

Nous disposons de plus de 30 000 composants différents, disponibles dans des machines de Pick and Place. En créant un fichier de fabrication en .pos, il permet aux machines de connaître quel composant est à placer à telle coordonnée et telle orientation.

En plus de ce fichier, il est nécessaire d’ajouter un fichier « gerber » correspondant aux emplacements où il faut placer de la pâte à souder. Une fois en place, la machine va pouvoir positionner les composants à l’emplacement désigné.

A l’issue, l’assemblage va dans un four à refusion. Refroidie, la carte est prête à être envoyée.

## Page 25

# VI. Projet de fabrication d’une soudeuse par point

## 1. Projet

Pour fabriquer nos propres batteries à partir de cellules 18650 de LiFePO4, il est nécessaire de les assembler à l’aide de bandes de zinc.

Pour les assembler nous avons plusieurs solutions :

− Le simple contact, comme des piles dans une télécommande.
Peu fiable dans un contexte de vibration et nous ne garantissons pas la surface de contact.
− La brasure étain.
Très bon contact mais chauffe les cellules ce qui peut les endommager
− La soudure par point.
Très bon contact, tenue mécanique excellente, mais besoin d’une machine spéciale

Le but de projet est donc de fabriquer une soudeuse par point principalement autour d’un transformateur de micro-onde. Ce type de transformateur, une fois rebobiné, peut délivrer une puissance de près d’un kilowatt avec un courant très fort (plusieurs centaines d’ampères) ce qui est idéal pour notre besoin.

Nous avons donc coupé l’enroulement secondaire que l’on a remplacé par plusieurs enroulements de câble de 25 mm² nous permettant d’avoir un transformateur abaisseur. Il a également fallu concevoir un système électronique pour commuter la puissance sur ce dernier pour en maitriser le fonctionnement.

## 2. Interface

L’interface homme machine sera réalisée par différents organes :

− Une pédale de déclenchement
− Un bouton de déclenchement situé sur le manche de soudure
− Un codeur rotatif muni d’un bouton central pour naviguer dans les menus − Un écran LCD 16x02 caractères
− Un buzzer
− Une interface USB

L’interface servira alors à pouvoir sélectionner les types de déclenchement, la puissance et l’énergie à délivrer.

## Page 26

## 3. Partie électronique

La partie électronique est simple. Nous utilisons un microcontrôleur de type ATMEGA328 alimenté par un régulateur à découpage isolé. Le microcontrôleur va contrôler un triac isolé grâce à un photo triac.

La puissance est modulée par un déclenchement par retard de phase et l’énergie est calculée grâce au nombre d’alternances commutées.

L’interface USB permettra de programmer l’AtMega.

## 4. Partie mécanique

La partie mécanique est elle aussi simple, la totalité du boitier est en bois. La façade avant ainsi que la façade arrière seront en MDF de 8mm d’épaisseur cela permettra de simplicité la fabrication des différentes encoches qui accueillerons les composants de l’interface homme machine, le casier de rangement, le port USB permettant la programmation et le codeur.

Les autres planches elles seront en contreplaqué de 16mm d’épaisseur afin d’assurer la rigidité du boîtier. Il est vrai que le transformateur a une masse non négligeable.

Une autre partie importante est la conception du refroidissement du boitier. Pour cela nous avons placé, à l’arrière du boîtier, un ventilateur de 90mm de diamètre, qui aspire l’air chaud du boitier et l’extrait en dehors de ce dernier.

Néanmoins il a fallu créer deux ouvertures afin de faire pénétrer l’air frais. Les composant nécessitant le plus d’être refroidi sont le transformateur et le triac. Dans cette optique les entrées d’air sont placées à l’avant du boitier. Ainsi l’air frais traverse l’ensemble du boîtier.

Pour assurer un refroidissement efficace nous avons fait en sorte que la surface de sortie de l’air chaud soit égal à la somme des surfaces d’entrée d’air.

Une dernière fonctionnalité est l’asservissement de la température en variant la vitesse de rotation du ventilateur.


## Page 27

Figure 15: vue 3D de l’avant de la soudeuse par point

Figure 16: vue 3D de l'arrière de la soudeuse par point

## Page 28

# VII. Synthèse

## 1. Difficultés

La principale difficulté a été l’apprentissage de l’ensemble des fonctionnalités du logiciel de CAO Kicad. Ce dernier est très complet et open source. Certaines fonctionnalités ne sont cependant pas simples à appréhender pour un débutant à la CAO en électronique.

Une autre difficulté a concerné la communication entre le chef de pôle en 4ème année et les autres membres de 3ème année. Entre autres difficultés, nous avions des journées bloquées pour le projet différent, régulièrement incompatibles avec les emplois du temps respectifs.

Au cours de la conception de certaines cartes, le cahier des charges pouvait changer, une partie du travail alors réalisée n’était plus nécessairement utile. Des situations de ce type pouvaient parfois être génératrices de perte de motivation. La seule consolation que l’on pouvait y trouver étaient quelles permettaient toutefois l’acquisition de nouvelles compétences.

La quasi-impossibilité de simuler lors de notre conception a également et mal vécu. Bien que notre chef de pôle ait rattrapé nos erreurs, nous sommes persuadés que nous aurions été meilleurs en conception si nous avions pu les effectuer avec une possibilité de simulation

## 2. Tâches à poursuivre

Les cartes sont prêtes, ne reste plus qu’à produire les prototypes et à les tester pour les transmettre au pôle informatique, afin qu’ils éprouvent à leur tour le soft développé auparavant.

Il sera nécessaire de construire les batteries à partir des cellules choisies.

Il aura également à réaliser l’électronique de la carte du bras qui, pour des raisons de choix des actionneurs, ne peut pas réellement être finalisée.

Un banc d’essai adaptable à LabVIEW devra également être réalisé afin de tester les différentes cartes, vérifier leur fonctionnement, leur consommation, la qualité des signaux qui transitent etc.

## 3. Rétrospective

Après un an passé au sein de Robotech Nancy, nous pouvons affirmer que ce projet est complet. Nous sommes très satisfaits et heureux d’avoir choisi ce projet. Nous encourageons les étudiants motivés et ayant une soif d’apprendre à intégrer ROBOTECH pour les prochaines années.

## Page 29

Nous avons développé de nombreuses compétences en termes de conception électronique. Nous avons mis en pratique nos cours et nous nous sommes améliorés sur le respect d’un planning, de la restitution de livrables et dans la communication interne comme externe au pôle.

Le fait d’être indépendants a été bénéfique. Nous avons pu susciter une forte entraide entre les membres de notre pôle, même si certains étaient déjà particulièrement à l’aise avec les logiciels et les méthodes utilisées.

Le projet Robotech Nancy est un projet avec 17 étudiants. Il n’est pas anormal que des dysfonctionnements se fassent jour d’un point de vue organisationnel. Néanmoins avec la volonté de chacun, des automatismes se sont mis en place et des méthodes de travail ont émergé. Aujourd’hui nous sommes efficaces et prêts à relever le défi : terminer notre robot, et, comme le dit notre tuteur M. NOIZETTE « exploser la compétition » !

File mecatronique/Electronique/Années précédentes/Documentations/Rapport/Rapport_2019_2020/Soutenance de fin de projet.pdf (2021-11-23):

# Soutenance de fin de projet

# Projet robotique - Pôle électronique


## Clyde-Borel KUIATE BOGNE François SULER

## Malek AYEB Maxence THIEBAUT

# Pôle électronique


## Sommaire

## I. Hiérarchie II. Architecture de robot III. L'alimentation IV. Conception des cartes électroniques V. Fabrication des cartes électroniques VI. Projet de fabrication d’une soudeuse par point VII.Conclusion

## Hiérarchie


Figure 1 : Organigramme du pôle électronique

## Architecture de robot


Figure 2 : Architecture du robot (semestre 1)

Figure 3 : schéma de l'architecture du robot

## L'alimentation


Figure 5 : cellule 18650 LiFePO4

Figure 4 : BMS 7 cellules

Figure 6 : schéma fonctionnel de l'alimentation

# Conception des cartes électroniques


## La carte d'alimentation


Figure 7 : vue 3D de la carte de l'alimentation

## La carte moteur


Figure 8 : vue 3D de la carte moteur

# La carte de l'ascenseur

Carte Ascenseur

Organe | Nom du signal | I/O STM32F103 | Type pin
P2.1 | DIR_Moteur_P-A-P_2.1 | PB2
| STEP_Moteur_P-A-P_P2.1 | PA8 | TIM1_CH 1
| Fin_De_Course_P2.1 | PB14
P1.1 | PWM_Pince_P1.1 | PA0 | TIM2_CH 1
| PWM_Poignet_P1.1 | PA6 | TIM3_CH 1
Programmation | SWCLK | PA15
| SWDIO | PA14
| NRST | NRST
| SWO | PA16
BUS CAN | CAN_RX | PA12 (TX STM) | CAN
| CAN_TX | PA11 (RX STM) | CAN


Figure 9: Vue 3D de la carte

Tableau 1 : Brochage de la carte

## Le phare


Figure 10 : vue 3D de la carte du phare

Signaux d’entrés

Fin de course bas
Fin de course haut
Bouton activation
Bouton désactivation

Signaux de sorties

+DC Moteur élévation
+DC Moteur lampe
TDI
TDO
TMS
TCK
Signaux bidirectionnels | CAN Low
| CAN Hight

Tableau 2 : Signaux des entrées et sorties

# La carte d'odométrie


Figure 11 : photos de la carte d'odométrie

## La carte communication


Figure 12 : Vue 3D de la carte de communication

Signaux d’entrés

MOSI

UART TX Raspi
CE0
SWIO
SWCLK
SWO
MCU RST

Signaux de sorties

MISO
SCLK
UART RX Raspi

Signaux bidirectionnels

CAN Low
CAN Hight

Tableau 3 : Signaux des entrées et sorties

## Fabrication des cartes électroniques


Figure 13 : LPKF S103 | Figure 14 : JLC PCB

## Projet de fabrication d’une soudeuse par point


Figure 15 : vue 3D de l'avant de la soudeuse par point | Figure 16 : vue 3D de l'arrière de la soudeuse par point

## Projet de fabrication d’une soudeuse par point


Figure 18 : vue 3D de la carte de puissance de la soudeuse par point

Figure 17 : vue 3D de la carte de commande de la soudeuse par point

# Conclusion


# Merci de votre attention !


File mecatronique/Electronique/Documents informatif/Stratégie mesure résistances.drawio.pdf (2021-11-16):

Méthode pont diviseur de tension avec Vref = 1k

Résistance | Tension sur la pin Analogique | Valeur DAC Arduino (10 bits) 0-1024 | Valeur DAC Nucleo (12 bits) 0-4096
Jaune : 470 Ohms | 1,598 V | 327 | 1309
Violette : 1000 Ohms | 2,500 V | 512 | 2048
Résistance à ne pas prendre : 4700 Ohm | 4,122 V | 840 | 3377

5V

## Analog pin

## Rref

R

## Important : - Recalculer les valeurs pour Rref réel - Prendre en compte la précision des résistances

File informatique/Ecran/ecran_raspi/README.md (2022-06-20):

# Le code permet de réaliser :

- la communication entre l'écran STM32F746G-DISCO et la RaspberryPi (envoi/réception de trames)

> *Remarque :* Tous les codes sont écrits en style **C/C++**

# Format de la trame des messages envoyés à l'écran :

| Mode | Catégorie | Sous-Catégorie | Data | Fin de trame  |
| --- | --- | --- | --- | --- |
| *1 octet* | *1 octet* | *1 octet* | *X octet* | *2 octets*  |
| `C` | `I` | `O/B/X/C` | `<value>` | `0x0A 0x0D` |
| `M` | `T/X/P/S/C/L/M/G` | `<selon categorie>` | `<value>` | `0x0A 0x0D` |

**Descriptions :**

- *[mode]*            :     `M (maintenance)` / `C (compétition)`
- *[catégorie]*      :

  {maintenance}

  - `C (bus CAN)` - `L (Lidar)` - `M (moteurs PAP)` - `G (gyroscope/capt. optique)`
  - `T (capteurs ToF)` - `X (xbee)` - `P (pompe à vide)` - `S (servomoteur)`

  {compétition} -> `I (initialisation)` - `S (score)` - `E (choix equipe)`
- *[sous-catégorie]* :

  {maintenance} -> `numéro du capteur ou de la carte`

  {initialisation} -> `O (odométrie)` - `B (base roulante)` - `X (xbee)` - `C (bus CAN)`

  {score} -> `P (score petit robot)` - `G (score grand robot)` - `T (score total)`

# Installation du code (sous Linux x86-64) :

```bash
git clone https://github.com/RobotechNancy/2021-2022.git
```

[**Username** : votre nom d'utilisateur GitHub]

[**Password** : vous devez générer un personal access token dans `Github -> Settings -> Developer Settings -> Personal Access Token -> Generate new token`]

```bash
cd 2021-2022/Pôle\ informatique/Communication/Communication\ inter-robots/xbee/  

g++ *.cpp -std=c++17 -o output

./output
```

# Publication d'une nouvelle version du code :

```bash
git pull && git add * && git commit -m "Version XX.XXR" && git push
```

[**Username** : votre nom d'utilisateur GitHub]

[**Password** : vous devez générer un personal access token dans `Github -> Settings -> Developer Settings -> Personal Access Token -> Generate new token`]

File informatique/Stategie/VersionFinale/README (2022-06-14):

Le code déposé contient les structures utilisées dans le moteur de graphe : la structure ARC ne sera pas utilisée, Etat est basiquement la structure de l'état, etc.

Les fichiers MesFonctions sont des fichiers de tests qui permettaient de simuler le fonctionnement du moteur.

Dans le main ici nous cherchons à importer la strucutre d'un grafcet depuis un fichier extérieur de type xml et de générer les intances de classes depuis le fichier et à partir des fichiers structures.
-> 3 fichiers xml de travail sont disponibles, grapheEnfant est un "brouillon" / test pour la mise en place des graphes enfants parents
-> Parser utilisé : RapidXML

Après l'idée est de regarder en temps réel si des transitions sont validées sur l'état courant
-> SI OUI passer la transition = changement d'état courant
-> SI NON mettre à jour les données de temporisation et de bouclage de l'état

A chaque passage de transition on met dans les logs les informations de passage de l'état (temps mis, boucle, condition de la transition passée)

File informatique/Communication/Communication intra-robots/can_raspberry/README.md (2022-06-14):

# Utilisation de la librairie can
```c++
Can can;  // crée un objet de la classe Can

int err = can.init(CAN_ADDR_RASPBERRY_E); // initialise le bus can avec l'adresse CAN_ADDR_RASPBERRY_E
if(err <0){
  can.logC << "erreur dans l'init du bus can. err n°" << dec << err << "\t\t c.f. #define" << mendl;
  return err;
}

can.start_listen(); // demarre un thread qui écoute les messages sur le bus can

uint8_t data[8] = {0x01,0x02,0xFF,0x34,0x45};
err = can.send(CAN_ADDR_BASE_ROULANTE, DEPLACEMENT_COURROIE, data, 5, true, 5); // envoie data à la base roulante 

while(!can.is_message(1)){ // attend un message d'id 1
}

CanResponse_t msg = can.get_message(1); // récupère le message d'id 1
```

### pour envoyer un message dans le bus can : 
```c++
can.send(CAN_ADDR addr, CAN_CODE_FCT codeFct , uint8_t data[], uint data_len, bool isRep, uint repLenght, uint idmessage);
```

### pour recevoir un message dans le bus can :
```c++
can.is_message(1)
```
cette fonction renvoie vrai si il y a un message d'id **1** en attente venant du bus can

```c++
CanResponse_t msg = can.get_message(1);
```
cette fonction permet de recuperer le message du buffer et le sortir du buffer 
>`is_message(1)` renvera toujours vrai tant que le message est dans le buffer et donc tant que `get_message(1)` n'est pas appeler

pour crée un bus can virtuel (vcan0) :
  - sudo modprobe vcan
  - sudo ip link add dev vcan0 type vcan
  - sudo ip link set up vcan0

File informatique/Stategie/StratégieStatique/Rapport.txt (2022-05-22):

FAITS :
- voir ce qu'il faut faire dans le mode auto_test

- CAN :
-> send(uint addr, uint codeFct , uint8_t data[], uint dataLen, bool isRep, uint repLenght)
-----)send(CAN_ADDR_BASE_ROULANTE, AVANCE, data, 5, true, 5)

A FAIRE 

- CAN :
-> Voir comment fonctionne le listen avec le can

- Imaginer l'algo du mode compétition
- Que faire dans le mode Arrêt d'urgence ? Proposer la possibilité de revenir sur l'étape précédente ? Gérer l'appui sur le bouton AU.
-> Faire une fonction utilisée dans le mode arrêt d'urgence qui permet le retour à l'étape cancel.

- Faire un gros header qui permet d'appeler un code fonction pour une carte donnée

- Faire un algo pour déduire le déplacement à faire pour rejoindre zone x
Procédé :
-> Demander la position (send, listen, analyser)
-> Appeler une fonction qui va retourner le déplacement (paramètres : position, lieu destination /!\ Faire des structures ?)
-> Envoyer les instructions de déplacement à la BR (faire les codes fonctions [vitesse, direction, distance], gérer les paramètres)
-> 

- Dans le cas où les 2 robots fonctionnent faire sur chaques cartes les fonctions R1 et R2
-> Dans le cas où au moins 1 robot lache faire R1 ou R2 pour l'autre et stratégieNOrobot sur l'autres / les autres

- Changer la fonction qui donne la disposition des 2 points et prendre en compte le scas où c'est égal
- Voir pour le décalage de 6° dans les calculs pour les déplacement hauts gauche et droite

V-  Ne pas mettre de réajustement mais faire une fonction oriente qui s'oriente bien pour finir
-> angles depart, arrivee 
-> 180 90

- Trame : Vitesse: 1 octet -> 
	  Direction : 1 octet -> 4 bits (voir 3 si on ne considère pas le 00000000)
	  Distance : 1 angle -> 2 octets -> 0 to 360
		     1 distance -> 2 octets (1?) -> 0 to x mm
- Trame Pompe : pas besoin de données
-> Lier les trames pour la pompe et le moteur pas à pas (PAS DE PARAMETRES) :=
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

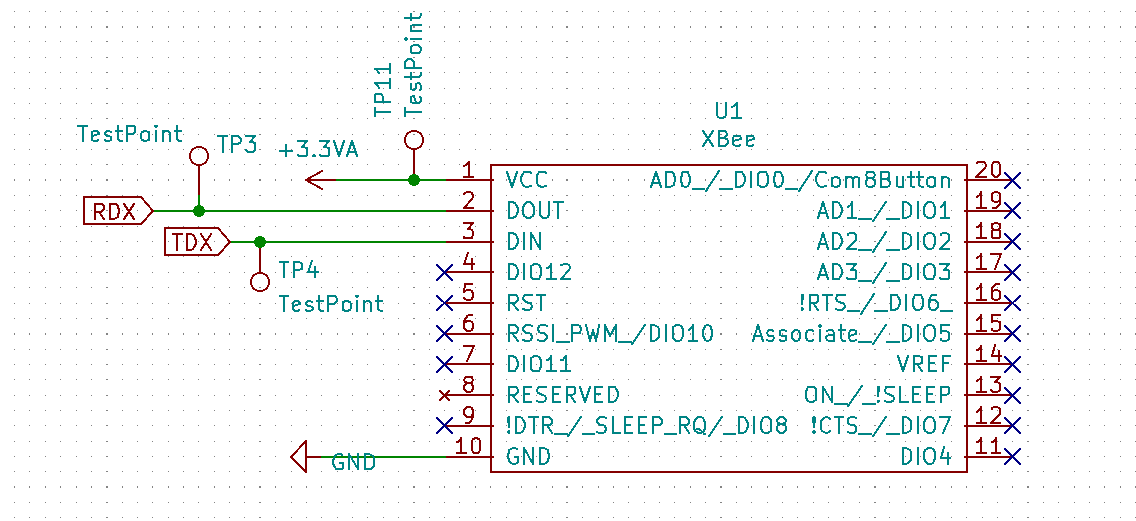
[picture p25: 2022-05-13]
mecatronique/Electronique/Documents informatif/Documentation/Pinout/Xbee.png

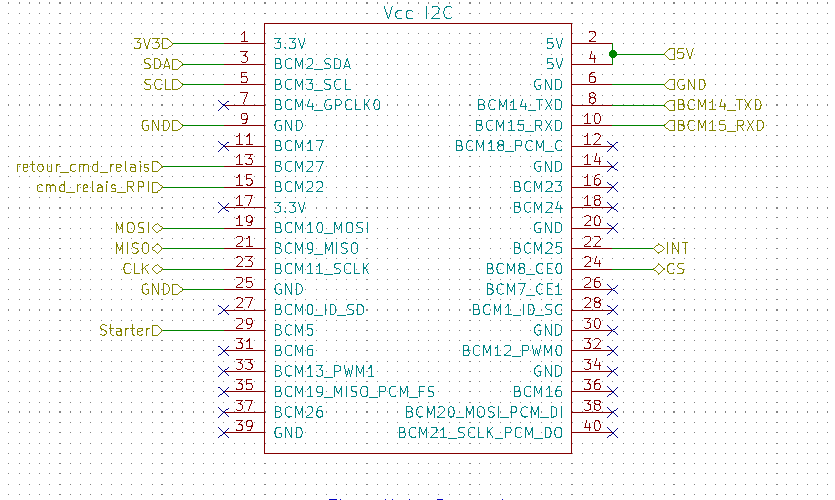
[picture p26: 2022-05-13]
mecatronique/Electronique/Documents informatif/Documentation/Pinout/Hat Raspberry.png

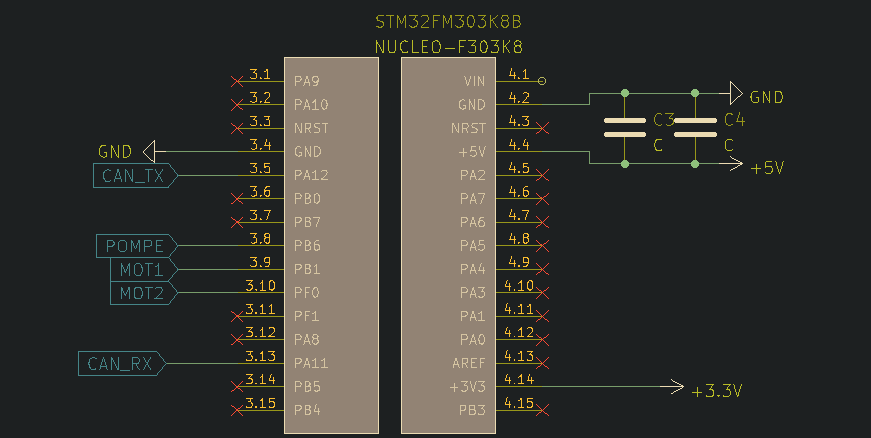
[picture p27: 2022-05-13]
mecatronique/Electronique/Documents informatif/Documentation/Pinout/Pinout actionneur grand robot.png

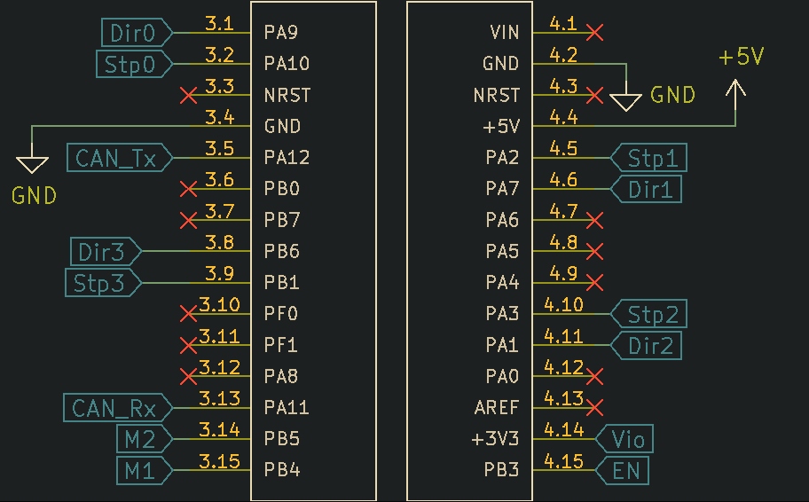
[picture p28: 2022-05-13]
mecatronique/Electronique/Documents informatif/Documentation/Pinout/Pinout BR.png

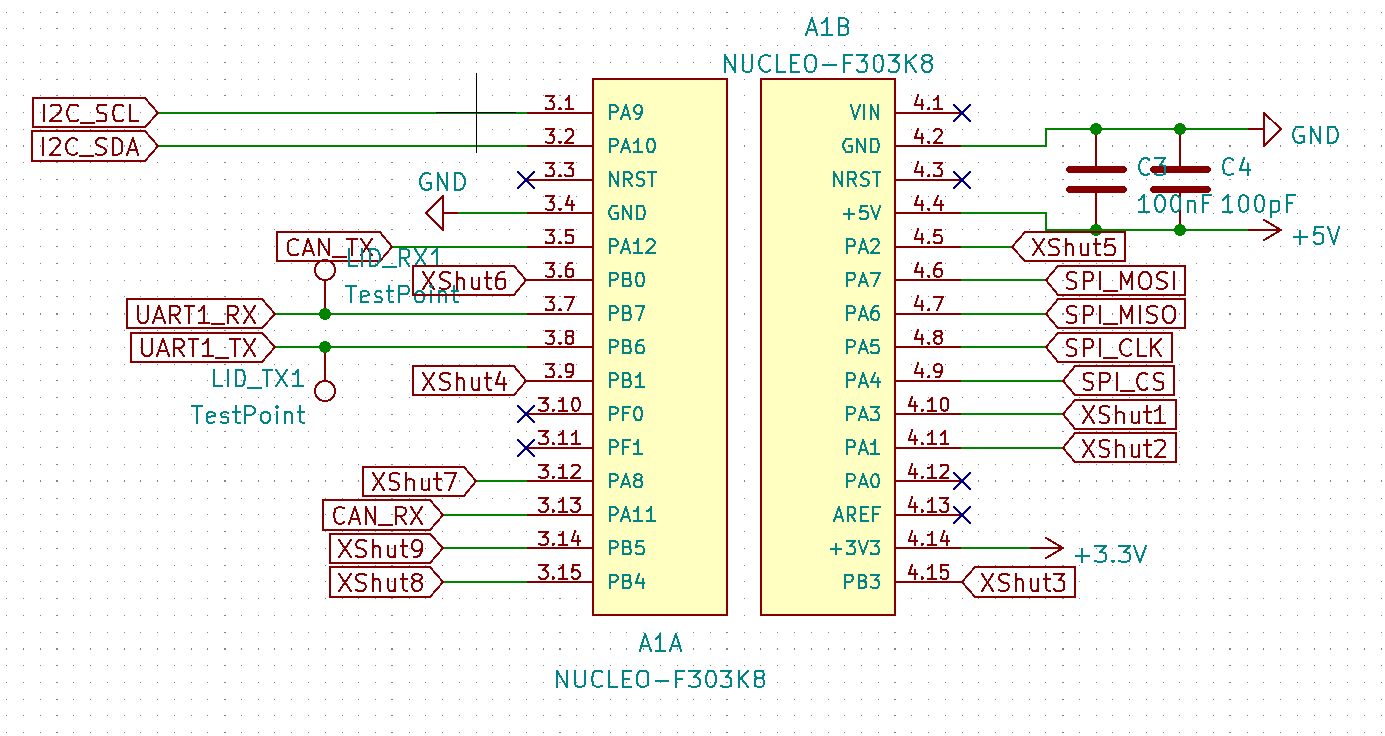
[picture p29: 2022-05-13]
mecatronique/Electronique/Documents informatif/Documentation/Pinout/carte ODOmètrie.png

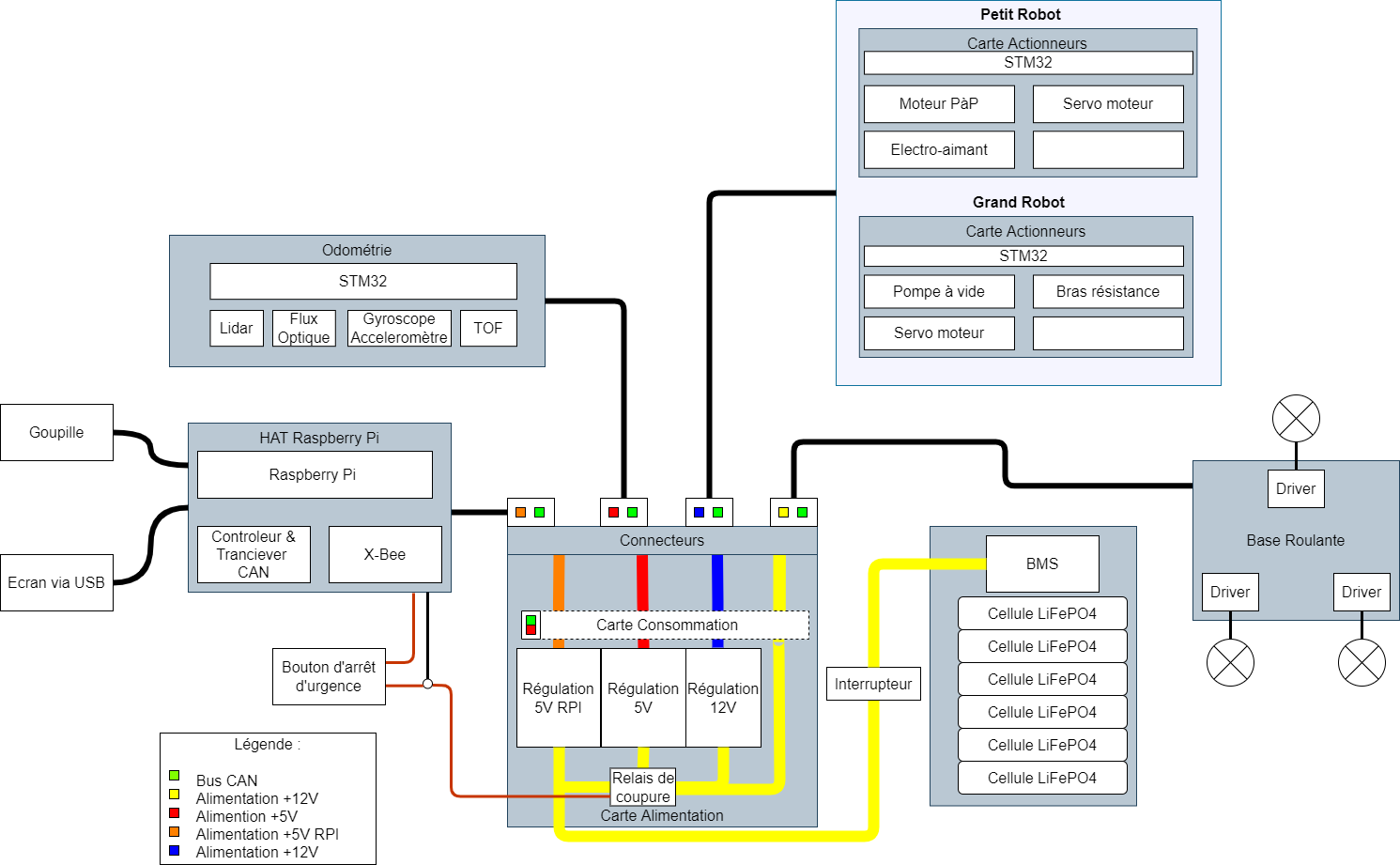
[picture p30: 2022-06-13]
mecatronique/Electronique/Documents informatif/Architecture Système.png

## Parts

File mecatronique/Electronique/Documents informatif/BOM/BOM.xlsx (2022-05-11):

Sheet: Version Kicad
BR
Id | Références | Boîtier | Quantité | Désignation | Fournisseur et rÃ©f
1 | NUCLEO-F303K8T1 | MODULE_NUCLEO-F303K8 | 1 | NUCLEO-F303K8
2 | J2,J3,J5,J4 | PinSocket_1x04_P2.54mm_Vertical | 4 | Conn_01x04_Female
3 | Driver1,Driver2,Driver4,Driver3 | MODULE_TMC2208_SILENTSTEPSTICK | 4 | TMC2208
4 | U1 | Converter_DCDC_RECOM_R-78E-0.5_THT | 1 | R-78E5.0-0.5
5 | SW1 | Switch_3_Pin | 1 | SW_Push_SPDT
6 | J1 | Alim_CablÃ©e_2_fils | 1 | Conn_01x04_Male
7 | H2,H1,H4,H3 | MountingHole_2.2mm_M2_ISO7380 | 4 | MountingHole
8 | G***,G*** | logoRobotechNancy10x10 | 2 | LOGO
9 | R_CAN1 | R_Axial_DIN0207_L6.3mm_D2.5mm_P7.62mm_Horizontal | 1 | R
10 | C8,C6,C9,C7 | CP_Radial_D8.0mm_P3.50mm | 4 | 220 Ã 1000 ÂµF
11 | TP11,TP5,TP9,TP7,TP8,TP10,TP2,TP1,TP3,TP6,TP4 | TestPoint_Pad_D2.0mm | 11 | TestPoint
12 | C2 | C_1206_3216Metric_Pad1.33x1.80mm_HandSolder | 1 | 100pF
13 | J5-CAN1 | JST_PH_B2B-PH-K_1x02_P2.00mm_Vertical | 1 | Conn_01x02_Female
14 | U2 | DIP-8_W7.62mm | 1 | MCP2551-I-P
15 | C1 | C_1206_3216Metric_Pad1.33x1.80mm_HandSolder | 1 | 100nF
16 | C4,C3 | C_1206_3216Metric_Pad1.33x1.80mm_HandSolder | 2 | 10u
17 | C5 | C_1206_3216Metric_Pad1.33x1.80mm_HandSolder | 1 | 100n
18 | REF** | TestPoint_Pad_D2.0mm | 1 | TestPoint_Pad_D2.0mm
Alimentation
Id | Références | Boîtier | Quantité | Désignation
1 | J1,J2,J3 | JST_PH_B4B-PH-K_1x04_P2.00mm_Vertical | 3 | Conn_01x04
2 | J4,J5 | JST_PH_B5B-PH-K_1x05_P2.00mm_Vertical | 2 | Conn_01x05
3 | K1 | Relay_SPDT_Omron-G5LE-1 | 1 | G5LE-1
4 | U2,U1 | Converter_DCDC_TRACO_TSR-1_THT | 2 | TSR_2-2450
5 | U3 | Converter_DCDC_TRACO_TSR-1_THT | 1 | TSR_2-24120
6 | J7 | PinSocket_2x10_P2.54mm_Vertical | 1 | Conn_02x10_Odd_Even
7 | J6 | Hirose_DF11-6DP-2DSA_2x03_P2.00mm_Vertical | 1 | Conn_02x03_Odd_Even
8 | D1 | D_DO-15_P12.70mm_Horizontal | 1 | D
9 | R1 | R_Axial_DIN0207_L6.3mm_D2.5mm_P10.16mm_Horizontal | 1 | 1600
10 | REF**,REF**,REF**,REF** | MountingHole_3.2mm_M3 | 4 | MountingHole_3.2mm_M3
11 | J8 | AMASS_XT30PW-M_1x02_P2.50mm_Horizontal | 1 | 24V in
12 | J9 | AMASS_XT30PW-M_1x02_P2.50mm_Horizontal | 1 | 24V out
13 | G***,G*** | logoRobotechNancy10x10 | 2 | LOGO
14 | Q1 | TO-126-3_Vertical | 1 | BD135
15 | J10 | JST_PH_B2B-PH-K_1x02_P2.00mm_Vertical | 1 | 24V in
16 | F2,F3,F1 | Fuse_Littelfuse_372_D8.50mm | 3 | 500mA
17 | C1 | CP_Radial_D5.0mm_P2.00mm | 1 | 22uF
18 | SW1 | Switch_3_Pin | 1 | SW_DPDT_x2
19 | TP13,TP8,TP14,TP7,TP1,TP6,TP4,TP9,TP11,TP2,TP12,TP5,TP10,TP3 | TestPoint_Pad_D2.0mm | 14 | TestPoint
20 | R3,R2 | R_Axial_DIN0207_L6.3mm_D2.5mm_P10.16mm_Horizontal | 2 | 120
HAT
Id | Références | Boîtier | Quantité | Désignation
1 | , | RPi_Hat_Mounting_Hole | 2
2 | J6 | Pin_Header_Straight_2x20 | 1 | Vcc I2C
3 | REF**,REF**,REF**,REF** | C_1206_3216Metric | 4 | C_1206_3216Metric
4 | TP6,TP12,TP14,TP7,TP9,TP8,TP5,TP10,TP13,TP11,TP4,TP3,TP1,TP2 | TestPoint_Pad_D1.0mm | 14 | TestPoint
5 | J2 | JST_PH_B4B-PH-K_1x04_P2.00mm_Vertical | 1 | RPi_GPIO
6 | TP15,TP16 | TestPoint_Pad_D2.0mm | 2 | TestPoint
7 | U2 | SSOP-28_5.3x10.2mm_P0.65mm | 1 | MCP25625-x-SS
8 | J3 | JST_PH_B2B-PH-K_1x02_P2.00mm_Vertical | 1 | Goupille
9 | C2,C1 | C_Disc_D5.1mm_W3.2mm_P5.00mm | 2 | 100 nF
10 | R2 | R_Axial_DIN0207_L6.3mm_D2.5mm_P10.16mm_Horizontal | 1 | 5k
11 | Y1 | Crystal_HC50_Horizontal | 1 | 8MHz
12 | R1 | R_Axial_DIN0207_L6.3mm_D2.5mm_P2.54mm_Vertical | 1 | R
13 | J1 | JST_PH_B2B-PH-K_1x02_P2.00mm_Vertical | 1 | ArrÃªt d'urgence
14 | Test_INT | TestPoint_Pad_D1.0mm | 1 | TestPoint_Pad_D1.0mm
15 | C4,C3 | C_Disc_D5.1mm_W3.2mm_P5.00mm | 2 | 22 pF
16 | J4 | PinHeader_2x02_P2.54mm_Vertical | 1 | Tension I2C
17 | G***,G*** | logoRobotechNancy10x10 | 2 | LOGO
18 | J5 | Hirose_DF11-6DP-2DSA_2x03_P2.00mm_Vertical | 1 | I2C
19 | U1 | XBEE-20_THT | 1 | XBee
Acti Petit
Id | Références | Boîtier | Quantité | Désignation
1 | TEST_RES1 | PinSocket_1x02_P2.54mm_Vertical | 1 | Conn_01x02
2 | D1 | D_A-405_P12.70mm_Horizontal | 1 | D
3 | Electroaimant1 | JST_PH_B2B-PH-K_1x02_P2.00mm_Vertical | 1 | Conn_01x02
4 | SERVO1 | JST_PH_B3B-PH-K_1x03_P2.00mm_Vertical | 1 | Conn_01x03
5 | U1 | DIP-8_W7.62mm | 1 | MCP2551-I-P
6 | C5 | CP_Radial_D8.0mm_P3.50mm | 1 | 220 Ã 1000 ÂµF
7 | G*** | logoRobotechNancy10x10 | 1 | LOGO
8 | Transistor2 | TO-220-3_Horizontal_TabDown | 1 | IRFZ44NPBF
9 | R3 | R_Axial_DIN0207_L6.3mm_D2.5mm_P10.16mm_Horizontal | 1 | 10k
10 | DRIVER1 | MODULE_TMC2208_SILENTSTEPSTICK | 1 | TMC2208_SILENTSTEPSTICK
11 | MotPasAPas1 | PinSocket_1x04_P2.54mm_Vertical | 1 | Conn_01x04
12 | Q1 | TO-92_Inline | 1 | BC557
13 | REF**,REF**,REF**,REF** | MountingHole_3.2mm_M3 | 4 | MountingHole_3.2mm_M3
14 | R4 | R_Axial_DIN0207_L6.3mm_D2.5mm_P10.16mm_Horizontal | 1 | 180
15 | R1 | R_Axial_DIN0207_L6.3mm_D2.5mm_P10.16mm_Horizontal | 1 | 1k
16 | STM32FM303K8 | MODULE_NUCLEO-F303K8 | 1 | NUCLEO-F303K8
17 | BUS_CAN1 | JST_PH_B5B-PH-K_1x05_P2.00mm_Vertical | 1 | Conn_01x05
18 | R2 | R_Axial_DIN0309_L9.0mm_D3.2mm_P12.70mm_Horizontal | 1 | R
19 | RESISTANCE1 | R_Axial_DIN0207_L6.3mm_D2.5mm_P10.16mm_Horizontal | 1 | 1000 Ohms
20 | TP9,TP3,TP11,TP13,TP16,TP5,TP1,TP14,TP10,TP2,TP8,TP15,TP4,TP12,TP6,TP7 | TestPoint_Pad_D2.0mm | 16 | TestPoint
21 | C4,C1 | C_1206_3216Metric | 2 | 1ÂµF
22 | C2,C3 | C_1206_3216Metric | 2 | 1pF
Act Grand
Id | Références | Boîtier | Quantité | Désignation
1 | ,,,, |  | 5
2 | BUS_CAN1 | JST_PH_B5B-PH-K_1x05_P2.00mm_Vertical | 1 | Conn_01x05
3 | STM32FM303K8 | MODULE_NUCLEO-F303K8 | 1 | NUCLEO-F303K8
4 | R1 | R_Axial_DIN0207_L6.3mm_D2.5mm_P10.16mm_Horizontal | 1 | 1k
5 | Q1 | TO-92_Inline | 1 | BC557
6 | D1 | D_A-405_P12.70mm_Horizontal | 1 | D
7 | R4 | R_Axial_DIN0207_L6.3mm_D2.5mm_P10.16mm_Horizontal | 1 | 180
8 | SERVO2,SERVO1 | JST_PH_B3B-PH-K_1x03_P2.00mm_Vertical | 2 | Conn_01x03
9 | R2 | R_Axial_DIN0309_L9.0mm_D3.2mm_P12.70mm_Horizontal | 1 | R
10 | G*** | logoRobotechNancy10x10 | 1 | LOGO
11 | TP1,TP4,TP8,TP7,TP2,TP6,TP5,TP3 | TestPoint_Pad_D2.0mm | 8 | TestPoint
12 | PompeAVide1 | JST_PH_B2B-PH-K_1x02_P2.00mm_Vertical | 1 | Conn_01x02
13 | R3 | R_Axial_DIN0207_L6.3mm_D2.5mm_P10.16mm_Horizontal | 1 | 10k
14 | U2 | TO-220-3_Horizontal_TabDown | 1 | IRFZ44NPBF
15 | U1 | DIP-8_W7.62mm | 1 | MCP2551-I-P
16 | JS1 | Molex_Micro-Fit_3.0_43650-0300_1x03_P3.00mm_Horizontal | 1 | Molex_Micro-Fit_3.0_1x03_P3.00mm
17 | C2,C4,C3,C1 | C_1206_3216Metric | 4 | C
Odo
Id | Références | Boîtier | Quantité | Désignation
1 | R2,R3,R1 | R_Axial_DIN0207_L6.3mm_D2.5mm_P10.16mm_Horizontal | 3 | R
2 | BUS_CAN1,TOF1 | JST_PH_B4B-PH-K_1x04_P2.00mm_Vertical | 2 | Conn_01x04
3 | Capt_Optiq1 | JST_PH_B7B-PH-K_1x07_P2.00mm_Vertical | 1 | Conn_01x07
4 | LIDAR | JST_PH_B5B-PH-K_1x05_P2.00mm_Vertical | 1 | Conn_01x05
5 | J1 | PinSocket_1x08_P2.54mm_Vertical | 1 | Conn_01x08
6 | G*** | logoRobotechNancy10x10 | 1 | LOGO
7 | A1 | MODULE_NUCLEO-F303K8 | 1 | NUCLEO-F303K8
8 | J5 | PinSocket_1x07_P2.54mm_Vertical | 1 | Conn_01x07
9 | U1 | DIP-8_W7.62mm | 1 | MCP2551-I-P
10 | REF,REF,REF,REF | MountingHole_3.2mm_M3 | 4 | MountingHole_3.2mm_M3
11 | SPI_MISO1,I2C_SDA1,+5V1,Can_RX1,I2C_SCL1,Can_H1,LID_RX1,SPI_CS1,Can_TX1,Can_L1,LID_TX1,GND1,SPI_CLK1,SPI_MOSI1 | TestPoint_Pad_D2.0mm | 14 | TestPoint
12 | C1,C2,C3,C4 | C_1206_3216Metric | 4 | C

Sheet: Feuil2
BR
Id | Références | Boîtier | Quantité | Désignation | Connecteurs :
1 | NUCLEO-F303K8T1 | MODULE_NUCLEO-F303K8 | 1 | NUCLEO-F303K8
2 | J2,J3,J5,J4 | PinSocket_1x04_P2.54mm_Vertical | 4 | Dupont x4 | Colonne1 | Colonne2 | Colonne3 | Colonne4 | Colonne5 | Colonne6 | Colonne7 | Colonne8 | Colonne9 | Colonne10 | Colonne11
3 | Driver1,Driver2,Driver4,Driver3 | MODULE_TMC2208_SILENTSTEPSTICK | 4 | TMC2208 | JST | BR | Alim | Hat | Petit | Grand | Odo | C. connecteur | Autres | Par robot : | Total :
4 | U1 | Converter_DCDC_RECOM_R-78E-0.5_THT | 1 | Régulateur 5V 500mA | x2 | 1 | 1 | 2 | 1 | 1 |  |  |  | 6 | 12
5 | SW1 | Switch_3_Pin | 1 | Interrupteur | x3 |  |  |  | 3 | 2 | 3 | 3 |  | 11 | 22
6 | J1 | Alim_CablÃ©e_2_fils | 1 | Empreinte câbles => XT30 mâle | x4 |  | 3 | 1 | 1 |  | 2 | 1 |  | 8 | 16
9 | R_CAN1 | R_Axial_DIN0207_L6.3mm_D2.5mm_P7.62mm_Horizontal | 1 | R | x5 |  | 2 |  | 1 | 1 | 1 | 5 |  | 10 | 20
10 | C8,C6,C9,C7 | CP_Radial_D8.0mm_P3.50mm | 4 | 220 Ã 1000 ÂµF | x7 |  |  |  |  |  | 1 |  |  | 1 | 2
12 | C2 | C_1206_3216Metric_Pad1.33x1.80mm_HandSolder | 1 | 100pF
13 | J5-CAN1 | JST_PH_B2B-PH-K_1x02_P2.00mm_Vertical | 1 | JST x2
14 | U2 | DIP-8_W7.62mm | 1 | MCP2551-I-P | Hirose |  | 1 | 1
15 | C1,C5 | C_1206_3216Metric_Pad1.33x1.80mm_HandSolder | 2 | 100nF
16 | C4,C3 | C_1206_3216Metric_Pad1.33x1.80mm_HandSolder | 2 | 10uF
 |  |  |  |  | Colonne1 | BR | Alim | Hat | Petit | Grand | Odo | Autres | Par robot : | Total :
 |  |  |  |  | Dupont | 78 | 20 | 44 | 48 | 30 | 45 |  | 265 | 530
Alimentation
Id | Références | Boîtier | Quantité | Désignation
1 | J1,J2,J3 | JST_PH_B4B-PH-K_1x04_P2.00mm_Vertical | 3 | JST x4
2 | J4,J5 | JST_PH_B5B-PH-K_1x05_P2.00mm_Vertical | 2 | JST x5
3 | K1 | Relay_SPDT_Omron-G5LE-1 | 1 | G5LE-1 | Résistance : | BR | Alim | Hat | Petit | Grand | Odo | Autres | Par robot : | Total :
4 | U2,U1 | Converter_DCDC_TRACO_TSR-1_THT | 2 | TSR_2-2450 | 120 Ω |  | 2 |  |  |  |  |  | 2 | 4
5 | U3 | Converter_DCDC_TRACO_TSR-1_THT | 1 | TSR_2-24120 | 1k Ω |  |  |  | 1 |  |  |  | 1 | 2
6 | J7 | PinSocket_2x10_P2.54mm_Vertical | 1 | Dupont mes courant | 1,6k Ω |  |  |  | 1 | 1 |  |  | 2 | 4
7 | J6 | Hirose_DF11-6DP-2DSA_2x03_P2.00mm_Vertical | 1 | Hirose 2x3 | 5k Ω |  |  | 1 |  |  |  |  | 1 | 2
8 | D1 | D_DO-15_P12.70mm_Horizontal | 1 | Diode | 10k Ω |  |  |  | 2 | 2 |  |  | 4 | 8
9 | R1 | R_Axial_DIN0207_L6.3mm_D2.5mm_P10.16mm_Horizontal | 1 | 1600
11 | J8 | AMASS_XT30PW-M_1x02_P2.50mm_Horizontal | 1 | XT30 femelle
12 | J9 | AMASS_XT30PW-M_1x02_P2.50mm_Horizontal | 1 | XT30 femelle
14 | Q1 | TO-126-3_Vertical | 1 | BD135
15 | J10 | JST_PH_B2B-PH-K_1x02_P2.00mm_Vertical | 1 | JST x2 | Condensateur : | BR | Alim | Hat | Petit | Grand | Odo | Autres | Par robot : | Total :
16 | F2,F3,F1 | Fuse_Littelfuse_372_D8.50mm | 3 | 500mA | C driver | 4 |  |  | 1 |  |  |  | 5 | 10
17 | C1 | CP_Radial_D5.0mm_P2.00mm | 1 | 22uF | 22pF |  |  | 2 |  |  |  |  | 2 | 4
18 | SW1 | Switch_3_Pin | 1 | Interrupteur | 100pF | 1 |  |  | 2 | 2 | 2 |  | 7 | 14
20 | R3,R2 | R_Axial_DIN0207_L6.3mm_D2.5mm_P10.16mm_Horizontal | 2 | 120 Ohm | 100nF | 2 |  | 2 | 2 | 2 | 2 |  | 10 | 20
 |  |  |  |  | 10µF | 2 |  |  |  |  |  |  | 2 | 4
HAT |  |  |  |  | 22µF |  | 1 |  |  |  |  |  | 1 | 2
Id | Références | Boîtier | Quantité | Désignation
2 | J6 | Pin_Header_Straight_2x20 | 1 | Dupont 2x20
5 | J2 | JST_PH_B4B-PH-K_1x04_P2.00mm_Vertical | 1 | JST x4
7 | U2 | SSOP-28_5.3x10.2mm_P0.65mm | 1 | MCP25625-x-SS
8 | J3 | JST_PH_B2B-PH-K_1x02_P2.00mm_Vertical | 1 | JST x2
9 | C2,C1 | C_Disc_D5.1mm_W3.2mm_P5.00mm ou C_1206_3216Metric | 2 | 100 nF
10 | R2 | R_Axial_DIN0207_L6.3mm_D2.5mm_P10.16mm_Horizontal | 1 | 5kOhm
11 | Y1 | Crystal_HC50_Horizontal | 1 | 8MHz
12 | R1 | R_Axial_DIN0207_L6.3mm_D2.5mm_P2.54mm_Vertical | 1 | R CAN
13 | J1 | JST_PH_B2B-PH-K_1x02_P2.00mm_Vertical | 1 | JST x2
15 | C4,C3 | C_Disc_D5.1mm_W3.2mm_P5.00mm ou C_1206_3216Metric | 2 | 22 pF
16 | J4 | PinHeader_2x02_P2.54mm_Vertical | 1 | Dupont 2x2
18 | J5 | Hirose_DF11-6DP-2DSA_2x03_P2.00mm_Vertical | 1 | Hirose 2x3
19 | U1 | XBEE-20_THT | 1 | XBee
Acti Petit
Id | Références | Boîtier | Quantité | Désignation
1 | TEST_RES1 | PinSocket_1x02_P2.54mm_Vertical | 1 | Dupont x2
2 | D1 | D_A-405_P12.70mm_Horizontal | 1 | D
3 | Electroaimant1 | JST_PH_B2B-PH-K_1x02_P2.00mm_Vertical | 1 | JST x2
4 | SERVO1 | JST_PH_B3B-PH-K_1x03_P2.00mm_Vertical | 1 | JST x 3
5 | U1 | DIP-8_W7.62mm | 1 | MCP2551-I-P
6 | C5 | CP_Radial_D8.0mm_P3.50mm | 1 | 220 Ã 1000 ÂµF
8 | Transistor2 | TO-220-3_Horizontal_TabDown | 1 | IRFZ44NPBF
9 | R3 | R_Axial_DIN0207_L6.3mm_D2.5mm_P10.16mm_Horizontal | 1 | 10k
10 | DRIVER1 | MODULE_TMC2208_SILENTSTEPSTICK | 1 | TMC2208_SILENTSTEPSTICK
11 | MotPasAPas1 | PinSocket_1x04_P2.54mm_Vertical | 1 | Dupont x4
12 | Q1 | TO-92_Inline | 1 | BC557
14 | R4 | R_Axial_DIN0207_L6.3mm_D2.5mm_P10.16mm_Horizontal | 1 | 180
15 | R1 | R_Axial_DIN0207_L6.3mm_D2.5mm_P10.16mm_Horizontal | 1 | 1k
16 | STM32FM303K8 | MODULE_NUCLEO-F303K8 | 1 | NUCLEO-F303K8
17 | BUS_CAN1 | JST_PH_B5B-PH-K_1x05_P2.00mm_Vertical | 1 | JST x5
18 | R2 | R_Axial_DIN0309_L9.0mm_D3.2mm_P12.70mm_Horizontal | 1 | R
19 | RESISTANCE1 | R_Axial_DIN0207_L6.3mm_D2.5mm_P10.16mm_Horizontal | 1 | 1000 Ohms
21 | C4,C1 | C_1206_3216Metric | 2 | 100nF
22 | C2,C3 | C_1206_3216Metric | 2 | 100pF
Act Grand
Id | Références | Boîtier | Quantité | Désignation
2 | BUS_CAN1 | JST_PH_B5B-PH-K_1x05_P2.00mm_Vertical | 1 | JST x5
3 | STM32FM303K8 | MODULE_NUCLEO-F303K8 | 1 | NUCLEO-F303K8
4 | R1 | R_Axial_DIN0207_L6.3mm_D2.5mm_P10.16mm_Horizontal | 1 | 1k
5 | Q1 | TO-92_Inline | 1 | BC557
6 | D1 | D_A-405_P12.70mm_Horizontal | 1 | D
7 | R4 | R_Axial_DIN0207_L6.3mm_D2.5mm_P10.16mm_Horizontal | 1 | 180
8 | SERVO2,SERVO1 | JST_PH_B3B-PH-K_1x03_P2.00mm_Vertical | 2 | JST x3
9 | R2 | R_Axial_DIN0309_L9.0mm_D3.2mm_P12.70mm_Horizontal | 1 | R
12 | PompeAVide1 | JST_PH_B2B-PH-K_1x02_P2.00mm_Vertical | 1 | JST x2
13 | R3 | R_Axial_DIN0207_L6.3mm_D2.5mm_P10.16mm_Horizontal | 1 | 10k
14 | U2 | TO-220-3_Horizontal_TabDown | 1 | IRFZ44NPBF
15 | U1 | DIP-8_W7.62mm | 1 | MCP2551-I-P
16 | JS1 | Molex_Micro-Fit_3.0_43650-0300_1x03_P3.00mm_Horizontal | 1 | Molex_Micro-Fit_3.0_1x03_P3.00mm
17 | C4,C1 | C_1206_3216Metric | 2 | 100nF
 | C2,C3 | C_1206_3216Metric | 2 | 100pF
Odo
Id | Références | Boîtier | Quantité | Désignation
1 | R2,R3,R1 | R_Axial_DIN0207_L6.3mm_D2.5mm_P10.16mm_Horizontal | 3 | R
2 | BUS_CAN1,TOF1 | JST_PH_B4B-PH-K_1x04_P2.00mm_Vertical | 2 | JST x4
3 | Capt_Optiq1 | JST_PH_B7B-PH-K_1x07_P2.00mm_Vertical | 1 | JST x7
4 | LIDAR | JST_PH_B5B-PH-K_1x05_P2.00mm_Vertical | 1 | JST x5
5 | J1 | PinSocket_1x08_P2.54mm_Vertical | 1 | Dupont x8
7 | A1 | MODULE_NUCLEO-F303K8 | 1 | NUCLEO-F303K8
8 | J5 | PinSocket_1x07_P2.54mm_Vertical | 1 | Dupont x7
9 | U1 | DIP-8_W7.62mm | 1 | MCP2551-I-P
 | C1,C3 | C_1206_3216Metric |  | 100nF
12 | C2,C4 | C_1206_3216Metric | 4 | 100pF
2 | BUS_CAN1,TOF1 | JST_PH_B4B-PH-K_1x04_P2.00mm_Vertical | 2 | JST x4

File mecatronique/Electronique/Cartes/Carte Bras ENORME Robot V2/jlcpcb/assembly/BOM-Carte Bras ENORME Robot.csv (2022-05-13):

Comment | Designator | Footprint | LCSC
Conn_01x05 | BUS_CAN1 | JST_PH_B5B-PH-K_1x05_P2.00mm_Vertical
NUCLEO-F303K8 | STM32FM303K8 | MODULE_NUCLEO-F303K8
1k | R1 | R_Axial_DIN0207_L6.3mm_D2.5mm_P10.16mm_Horizontal
BC557 | Q1 | TO-92_Inline
D | D1 | D_A-405_P12.70mm_Horizontal
180 | R4 | R_Axial_DIN0207_L6.3mm_D2.5mm_P10.16mm_Horizontal
Conn_01x03 | SERVO2 | JST_PH_B3B-PH-K_1x03_P2.00mm_Vertical
R | R2 | R_Axial_DIN0309_L9.0mm_D3.2mm_P12.70mm_Horizontal
Conn_01x02 | PompeAVide1 | JST_PH_B2B-PH-K_1x02_P2.00mm_Vertical
10k | R3 | R_Axial_DIN0207_L6.3mm_D2.5mm_P10.16mm_Horizontal
IRFZ44NPBF | U2 | TO-220-3_Horizontal_TabDown
MCP2551-I-P | U1 | DIP-8_W7.62mm
Molex_Micro-Fit_3.0_43650-0300_1x03_P3.00mm_Horizontal | JS1 | Molex_Micro-Fit_3.0_43650-0300_1x03_P3.00mm_Horizontal
Conn_01x03 | SERVO1 | JST_PH_B3B-PH-K_1x03_P2.00mm_Vertical
TestPoint | TP4 | TestPoint_Pad_D2.0mm
TestPoint | TP8 | TestPoint_Pad_D2.0mm
C | C2 | C_1206_3216Metric
TestPoint | TP7 | TestPoint_Pad_D2.0mm
TestPoint | TP2 | TestPoint_Pad_D2.0mm
C | C4 | C_1206_3216Metric
TestPoint | TP6 | TestPoint_Pad_D2.0mm
C | C3 | C_1206_3216Metric
C | C1 | C_1206_3216Metric
TestPoint | TP5 | TestPoint_Pad_D2.0mm
TestPoint | TP3 | TestPoint_Pad_D2.0mm

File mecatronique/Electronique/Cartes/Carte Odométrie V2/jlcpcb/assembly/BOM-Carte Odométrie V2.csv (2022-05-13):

Comment | Designator | Footprint | LCSC
Conn_01x07 | Giroscope1 | PinSocket_1x07_P2.54mm_Vertical
X3 | J3 | JST_PH_B3B-PH-K_1x03_P2.00mm_Vertical
Conn_01x04 | BUS_CAN1 | JST_PH_B4B-PH-K_1x04_P2.00mm_Vertical
INT | TP1 | TestPoint_Loop_D2.50mm_Drill1.0mm
Conn_01x07 | Capt_Optiq1 | JST_PH_B7B-PH-K_1x07_P2.00mm_Vertical
Conn_01x05 | LIDAR1 | JST_PH_B5B-PH-K_1x05_P2.00mm_Vertical
X1 | J2 | JST_PH_B3B-PH-K_1x03_P2.00mm_Vertical
X2 | J1 | JST_PH_B3B-PH-K_1x03_P2.00mm_Vertical
NUCLEO-F303K8 | A1 | MODULE_NUCLEO-F303K8
Conn_01x04 | TOF1 | JST_PH_B4B-PH-K_1x04_P2.00mm_Vertical
R | R3 | R_Axial_DIN0207_L6.3mm_D2.5mm_P10.16mm_Horizontal
Conn_01x08 | Accéleromètre1 | PinSocket_1x08_P2.54mm_Vertical
MCP2551-I-P | U1 | DIP-8_W7.62mm
TestPoint | SPI_MISO1 | TestPoint_Pad_D2.0mm
TestPoint | I2C_SDA1 | TestPoint_Pad_D2.0mm
TestPoint | Can_RX1 | TestPoint_Pad_D2.0mm
100pF | C1 | C_1206_3216Metric
100nF | C2 | C_1206_3216Metric
TestPoint | I2C_SCL1 | TestPoint_Pad_D2.0mm
TestPoint | Can_H1 | TestPoint_Pad_D2.0mm
TestPoint | LID_RX1 | TestPoint_Pad_D2.0mm
TestPoint | SPI_CS1 | TestPoint_Pad_D2.0mm
TestPoint | Can_TX1 | TestPoint_Pad_D2.0mm
TestPoint | Can_L1 | TestPoint_Pad_D2.0mm
100nF | C3 | C_1206_3216Metric
TestPoint | LID_TX1 | TestPoint_Pad_D2.0mm
100pF | C4 | C_1206_3216Metric
TestPoint | GND1 | TestPoint_Pad_D2.0mm
TestPoint | SPI_CLK1 | TestPoint_Pad_D2.0mm
TestPoint | SPI_MOSI1 | TestPoint_Pad_D2.0mm

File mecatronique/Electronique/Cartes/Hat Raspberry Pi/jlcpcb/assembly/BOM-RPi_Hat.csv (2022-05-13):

Comment | Designator | Footprint | LCSC
Vcc I2C | J6 | Pin_Header_Straight_2x20
TestPoint | TP6 | TestPoint_Pad_D1.0mm
RPi_GPIO | J2 | JST_PH_B4B-PH-K_1x04_P2.00mm_Vertical
TestPoint | TP12 | TestPoint_Pad_D1.0mm
TestPoint | TP15 | TestPoint_Pad_D2.0mm
TestPoint | TP14 | TestPoint_Pad_D1.0mm
TestPoint | TP7 | TestPoint_Pad_D1.0mm
MCP25625-x-SS | U2 | SSOP-28_5.3x10.2mm_P0.65mm
Goupille | J3 | JST_PH_B2B-PH-K_1x02_P2.00mm_Vertical
TestPoint | TP9 | TestPoint_Pad_D1.0mm
TestPoint | TP8 | TestPoint_Pad_D1.0mm
100 nF | C2 | C_Disc_D5.1mm_W3.2mm_P5.00mm
100 nF | C1 | C_Disc_D5.1mm_W3.2mm_P5.00mm
5k | R2 | R_Axial_DIN0207_L6.3mm_D2.5mm_P10.16mm_Horizontal
8MHz | Y1 | Crystal_HC50_Horizontal
R | R1 | R_Axial_DIN0207_L6.3mm_D2.5mm_P2.54mm_Vertical
Arrêt d'urgence | J1 | JST_PH_B2B-PH-K_1x02_P2.00mm_Vertical
22 pF | C4 | C_Disc_D5.1mm_W3.2mm_P5.00mm
TestPoint | TP5 | TestPoint_Pad_D1.0mm
TestPoint | TP10 | TestPoint_Pad_D1.0mm
Tension I2C | J4 | PinHeader_2x02_P2.54mm_Vertical
22 pF | C3 | C_Disc_D5.1mm_W3.2mm_P5.00mm
I2C | J5 | Hirose_DF11-6DP-2DSA_2x03_P2.00mm_Vertical
TestPoint | TP13 | TestPoint_Pad_D1.0mm
XBee | U1 | XBEE-20_THT
TestPoint | TP11 | TestPoint_Pad_D1.0mm
TestPoint | TP4 | TestPoint_Pad_D1.0mm
TestPoint | TP3 | TestPoint_Pad_D1.0mm
TestPoint | TP1 | TestPoint_Pad_D1.0mm
TestPoint | TP2 | TestPoint_Pad_D1.0mm
TestPoint | TP16 | TestPoint_Pad_D2.0mm

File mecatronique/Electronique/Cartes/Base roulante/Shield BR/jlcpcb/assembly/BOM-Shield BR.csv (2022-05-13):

Comment | Designator | Footprint | LCSC
Conn_01x04_Female | J2 | PinSocket_1x04_P2.54mm_Vertical
Conn_01x04_Female | J3 | PinSocket_1x04_P2.54mm_Vertical
Conn_01x04_Female | J5 | PinSocket_1x04_P2.54mm_Vertical
Conn_01x04_Female | J4 | PinSocket_1x04_P2.54mm_Vertical
TMC2208 | Driver1 | MODULE_TMC2208_SILENTSTEPSTICK
TMC2208 | Driver2 | MODULE_TMC2208_SILENTSTEPSTICK
TMC2208 | Driver4 | MODULE_TMC2208_SILENTSTEPSTICK
TMC2208 | Driver3 | MODULE_TMC2208_SILENTSTEPSTICK
R-78E5.0-0.5 | U1 | Converter_DCDC_RECOM_R-78E-0.5_THT
SW_Push_SPDT | SW1 | Switch_3_Pin
Conn_01x04_Male | J1 | Alim_Cablée_2_fils
MountingHole | H2 | MountingHole_2.2mm_M2_ISO7380
MountingHole | H1 | MountingHole_2.2mm_M2_ISO7380
MountingHole | H4 | MountingHole_2.2mm_M2_ISO7380
MountingHole | H3 | MountingHole_2.2mm_M2_ISO7380
R | R_CAN1 | R_Axial_DIN0207_L6.3mm_D2.5mm_P7.62mm_Horizontal
220 à 1000 µF | C8 | CP_Radial_D8.0mm_P3.50mm
220 à 1000 µF | C6 | CP_Radial_D8.0mm_P3.50mm
220 à 1000 µF | C9 | CP_Radial_D8.0mm_P3.50mm
TestPoint | TP11 | TestPoint_Pad_D2.0mm
100pF | C2 | C_1206_3216Metric_Pad1.33x1.80mm_HandSolder
Conn_01x02_Female | J5-CAN1 | JST_PH_B2B-PH-K_1x02_P2.00mm_Vertical
220 à 1000 µF | C7 | CP_Radial_D8.0mm_P3.50mm
MCP2551-I-P | U2 | DIP-8_W7.62mm
100nF | C1 | C_1206_3216Metric_Pad1.33x1.80mm_HandSolder
TestPoint | TP5 | TestPoint_Pad_D2.0mm
TestPoint | TP9 | TestPoint_Pad_D2.0mm
TestPoint | TP7 | TestPoint_Pad_D2.0mm
10u | C4 | C_1206_3216Metric_Pad1.33x1.80mm_HandSolder
TestPoint | TP8 | TestPoint_Pad_D2.0mm
100n | C5 | C_1206_3216Metric_Pad1.33x1.80mm_HandSolder
TestPoint | TP10 | TestPoint_Pad_D2.0mm
TestPoint | TP2 | TestPoint_Pad_D2.0mm
TestPoint | TP1 | TestPoint_Pad_D2.0mm
TestPoint | TP3 | TestPoint_Pad_D2.0mm
TestPoint | TP6 | TestPoint_Pad_D2.0mm
TestPoint | TP4 | TestPoint_Pad_D2.0mm
10u | C3 | C_1206_3216Metric_Pad1.33x1.80mm_HandSolder

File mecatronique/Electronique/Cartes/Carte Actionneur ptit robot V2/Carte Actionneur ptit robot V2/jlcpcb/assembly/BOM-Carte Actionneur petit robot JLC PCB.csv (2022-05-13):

Comment | Designator | Footprint | LCSC
Conn_01x02 | TEST_RES1 | PinSocket_1x02_P2.54mm_Vertical
D | D1 | D_A-405_P12.70mm_Horizontal
Conn_01x02 | Electroaimant1 | JST_PH_B2B-PH-K_1x02_P2.00mm_Vertical
Conn_01x03 | SERVO1 | JST_PH_B3B-PH-K_1x03_P2.00mm_Vertical
MCP2551-I-P | U1 | DIP-8_W7.62mm
220 à 1000 µF | C5 | CP_Radial_D8.0mm_P3.50mm
IRFZ44NPBF | Transistor2 | TO-220-3_Horizontal_TabDown
10k | R3 | R_Axial_DIN0207_L6.3mm_D2.5mm_P10.16mm_Horizontal
TMC2208_SILENTSTEPSTICK | DRIVER1 | MODULE_TMC2208_SILENTSTEPSTICK
Conn_01x04 | MotPasAPas1 | PinSocket_1x04_P2.54mm_Vertical
BC557 | Q1 | TO-92_Inline
180 | R4 | R_Axial_DIN0207_L6.3mm_D2.5mm_P10.16mm_Horizontal
1k | R1 | R_Axial_DIN0207_L6.3mm_D2.5mm_P10.16mm_Horizontal
NUCLEO-F303K8 | STM32FM303K8 | MODULE_NUCLEO-F303K8
Conn_01x05 | BUS_CAN1 | JST_PH_B5B-PH-K_1x05_P2.00mm_Vertical
R | R2 | R_Axial_DIN0309_L9.0mm_D3.2mm_P12.70mm_Horizontal
1000 Ohms | RESISTANCE1 | R_Axial_DIN0207_L6.3mm_D2.5mm_P10.16mm_Horizontal
TestPoint | TP9 | TestPoint_Pad_D2.0mm
1µF | C4 | C_1206_3216Metric
1µF | C1 | C_1206_3216Metric
TestPoint | TP3 | TestPoint_Pad_D2.0mm
TestPoint | TP11 | TestPoint_Pad_D2.0mm
TestPoint | TP13 | TestPoint_Pad_D2.0mm
TestPoint | TP16 | TestPoint_Pad_D2.0mm
TestPoint | TP5 | TestPoint_Pad_D2.0mm
TestPoint | TP1 | TestPoint_Pad_D2.0mm
TestPoint | TP14 | TestPoint_Pad_D2.0mm
1pF | C2 | C_1206_3216Metric
TestPoint | TP10 | TestPoint_Pad_D2.0mm
TestPoint | TP2 | TestPoint_Pad_D2.0mm
TestPoint | TP8 | TestPoint_Pad_D2.0mm
TestPoint | TP15 | TestPoint_Pad_D2.0mm
1pF | C3 | C_1206_3216Metric
TestPoint | TP4 | TestPoint_Pad_D2.0mm
TestPoint | TP12 | TestPoint_Pad_D2.0mm
TestPoint | TP6 | TestPoint_Pad_D2.0mm
TestPoint | TP7 | TestPoint_Pad_D2.0mm

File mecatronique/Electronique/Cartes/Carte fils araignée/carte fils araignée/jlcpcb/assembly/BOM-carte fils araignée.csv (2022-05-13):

Comment | Designator | Footprint | LCSC
X3 | J5 | JST_EH_B3B-EH-A_1x03_P2.50mm_Vertical
Conn_01x05 | J2 | JST_EH_S5B-EH_1x05_P2.50mm_Horizontal
TestPoint | I2C_SCL1 | TestPoint_Pad_D2.0mm
Conn_01x05 | J13 | JST_EH_S5B-EH_1x05_P2.50mm_Horizontal
Conn_01x05 | J11 | JST_EH_S5B-EH_1x05_P2.50mm_Horizontal
Conn_01x05 | J7 | JST_EH_B5B-EH-A_1x05_P2.50mm_Vertical
TestPoint | I2C_SDA1 | TestPoint_Pad_D2.0mm
Conn_01x05 | J10 | JST_EH_S5B-EH_1x05_P2.50mm_Horizontal
TestPoint | GND1 | TestPoint_Pad_D2.0mm
Conn_01x05 | J12 | JST_EH_S5B-EH_1x05_P2.50mm_Horizontal
X2 | J8 | JST_EH_B3B-EH-A_1x03_P2.50mm_Vertical
X1 | J6 | JST_EH_B3B-EH-A_1x03_P2.50mm_Vertical
Conn_01x05 | J1 | JST_EH_S5B-EH_1x05_P2.50mm_Horizontal
Conn_01x04 | J9 | JST_EH_B4B-EH-A_1x04_P2.50mm_Vertical
Conn_01x05 | J4 | JST_EH_S5B-EH_1x05_P2.50mm_Horizontal
Conn_01x05 | J3 | JST_EH_S5B-EH_1x05_P2.50mm_Horizontal

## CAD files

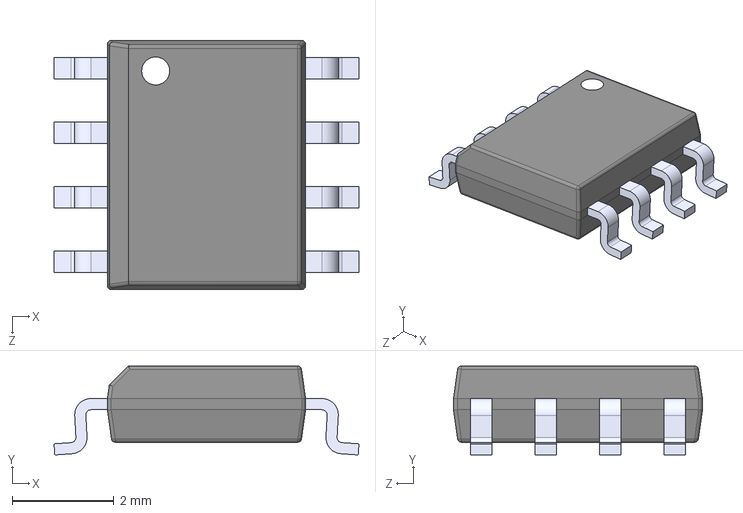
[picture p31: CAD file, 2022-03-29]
mecatronique/Electronique/Cartes/Base roulante/TCAN332D/TCAN332D.step
6.00 x 1.75 x 4.90 mm

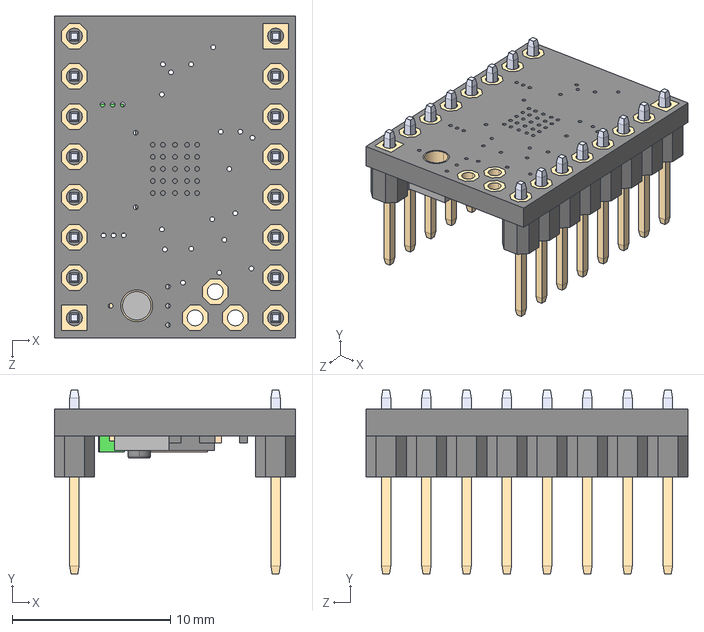
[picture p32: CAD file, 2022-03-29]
mecatronique/Electronique/Cartes/Base roulante/TMC2208_SILENTSTEPSTICK/TMC2208_SILENTSTEPSTICK.step
15.2 x 11.6 x 20.3 mm

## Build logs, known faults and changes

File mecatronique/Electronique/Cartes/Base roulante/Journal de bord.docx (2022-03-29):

# Journal de bord Base Roulante

## Début d’année :

L’équipe de l’année passée à réalisé une carte de contrôle de la base roulante. Celle-ci est directement alimentée par la batterie (donc jusqu’à 24V). La carte comprend des emplacements pour un microcontrôleur STM32 nucléo style Nano et quatre drivers pour moteur pas-à-pas. Nous devons régler un des problèmes de cette carte qui est que sont régulateur 24V-5V grille au bout d’un certain temps.

## Notre travail :

Nous avons vérifié la consommation des composants => tout est bon (<500mA)

Nous avons remarqué que les drivers sont alimentés en 3,3V par le microcontrôleur.

Il manquait deux condensateurs de filtrage montés en surface sur la carte électronique. Nous les avons donc soudés et nous avons ajouté une diode Zener de protection en sortie du régulateur.

Nous avons changé le régulateur défectueux par un neuf et testé le circuit. Un des driver faisait court-circuit, nous l’avons donc remplacé.

Nous avons finalement pu tester la carte avec ses différents composants. Les premiers tests ont été fait avec un STM32 avec un format différent que nous avons câblé sut la carte car le bon microcontrôleur été en cours de ravitaillement. Nous nous sommes rendu compte que les entrés STEP des drivers ne possédaient pas de résistance de pull up ou pull down. Nous devons donc configurer les sorties du microcontrôleur pour qu’elles intègrent ces résistances.

29/03/2022

La carte de la base roulante à été revue pour être réalisable à Polytech (plus grandes pistes/via, etc …) et un transceiver CAN MCP2551 à été ajouté.

Nous allons enlever les interrupteurs connectés aux pins EN, MS1 et MS2 pour les relier directement aux pins de la STM32. Il faut donc changer la tension d’alimentation logique des drivers pour passer de 3V3 à 5V (même tension logique que les sorties digitales de la STM32).

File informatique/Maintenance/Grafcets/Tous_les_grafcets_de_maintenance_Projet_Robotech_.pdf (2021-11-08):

## Grafcet de maintenance

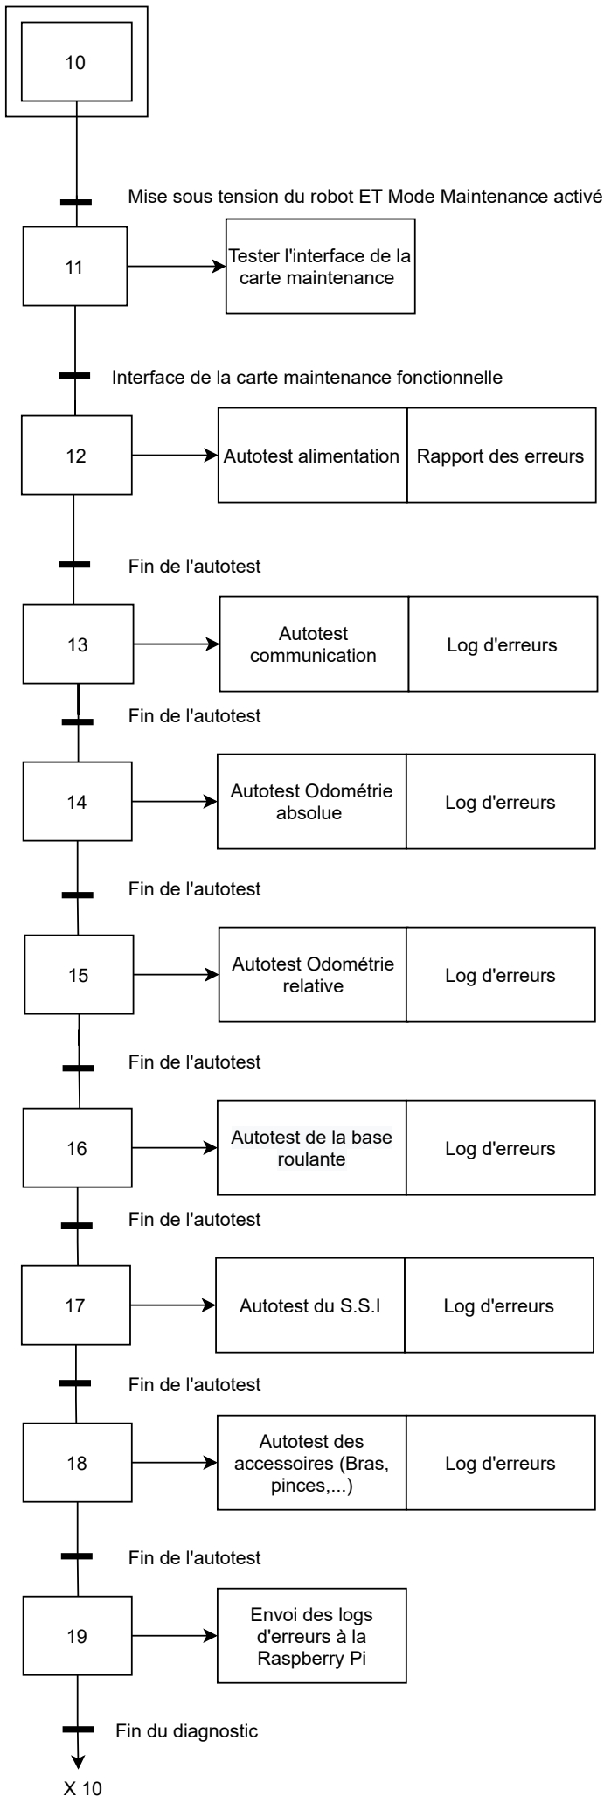
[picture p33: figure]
Rapport des erreurs; Tester l'interface de la carte maintenance; Autotest alimentation; Autotest; communication; Log d'erreurs; Fin de l'autotest; Autotest Odométrie; absolue; relative; Autotest de la base; roulante; Autotest du S.S.I; Autotest des accessoires (Bras, pinces,...); Envoi des logs d'erreurs à la Raspberry Pi; Fin du diagnostic

Mise sous tension du robot ET Mode Maintenance activé

Interface de la carte maintenance fonctionnelle

NB:
Tester l'interface de la carte maintenance implique tester les registres, le BUS CAN, tester si la carte n'est pas endommagée, tester si la carte nous envoie les logs d'erreurs ou pas...

S.S.I: Système de Sécurité Incendie sous forme de détecteur de début de défaillance.
En effet, dans le cas d'incendie, le courant débité par la batterie augmente d'une manière exponentielle (on détecte un excès de courant). Donc, il faut mettre en place des ampèremètres qui vont nous affichés les valeurs du courant tout au long de la compétition.

21 | Lancer le programme "Starting Test"
22 | Faire appel à la carte moteur

23

"starting Test" valide ET carte en mode maintenance

Translater le robot en
diagonale (haut et
bas), à vitesse
constante

Appel de la carte moteur fini

24

Grafcet Maintenance Capteurs optiques

Passer la carte en
mode maintenance

Appeler la fonction maintenance de la carte

Intégrer la carte moteur/
Appeler la carte moteur

Relever l'écart entre
les positions de
départ et de fin

Afficher " Capteur défaillant"

Petit écart entre les deux positions | Écart trop élevé entre les deux positions

Fin d'écriture et d'enregistrement

25

Fin d'enregistrement

26

Envoyer les
enregistrements à la
carte maintenance

Enregistrements envoyés

X20

Afficher:
"Capteur
Optique
opérationnel"

Enregistrer les
valeurs des
coordonées

NB: Le but de "Starting test" est d'étudier l'état du processeur et de la RAM , càd s'ils sont capables de stocker une variable, de calculer une autre, de les ressortir... De plus, l'objectif de ce test est de savoir si on est capable de faire le checksum de toutes les cartes.

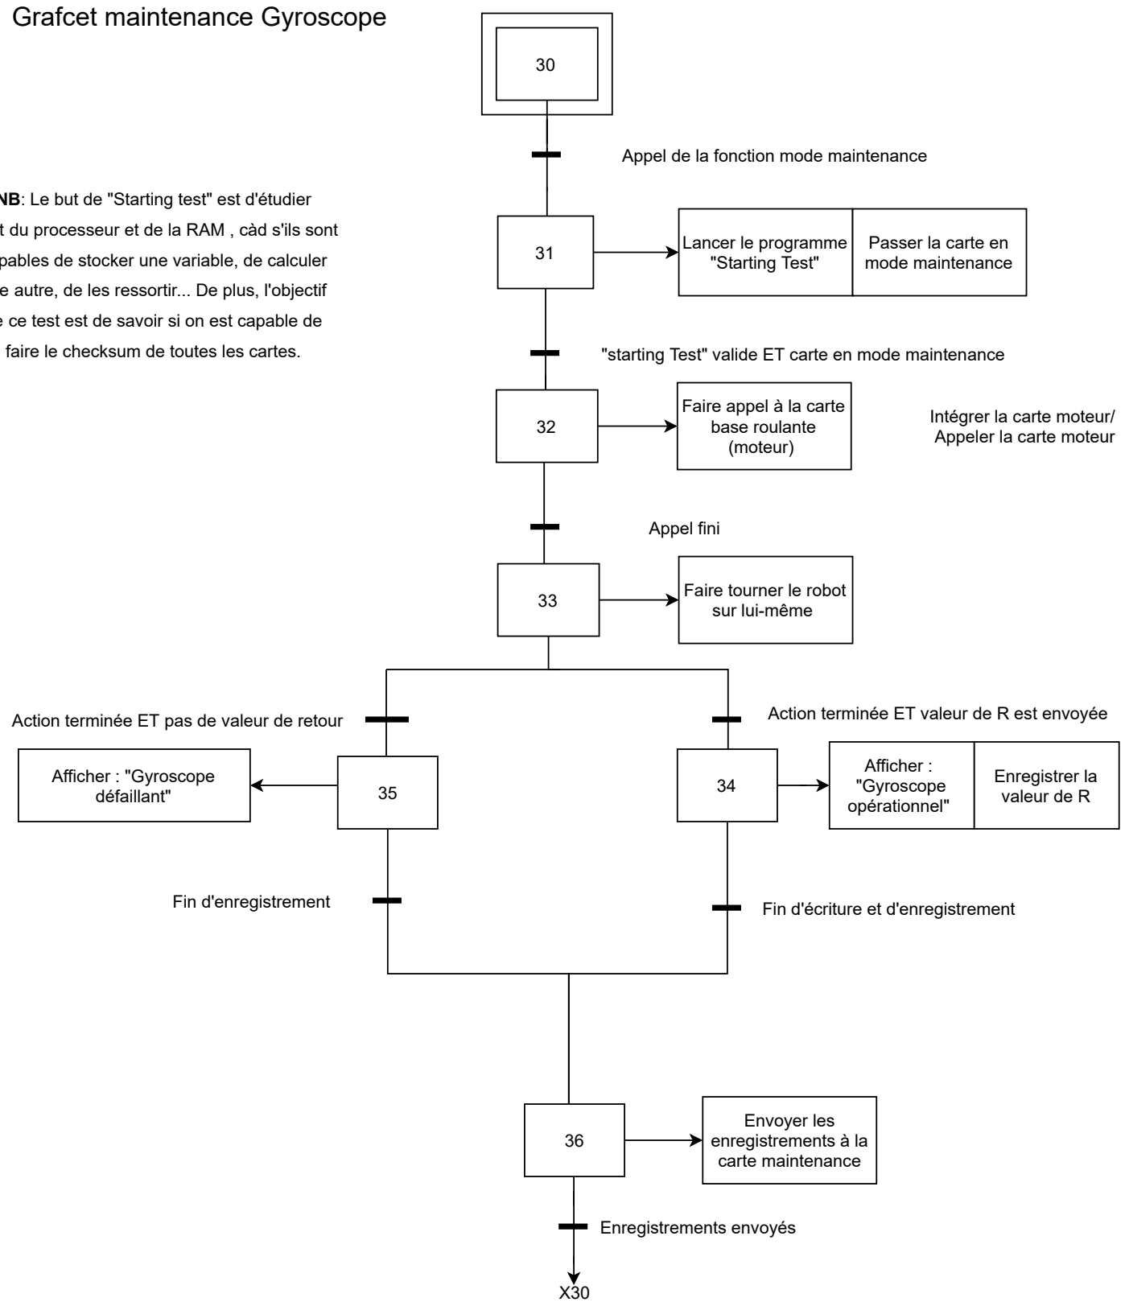
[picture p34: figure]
Grafcet maintenance Gyroscope; Lancer le programme; "Starting Test"; Faire appel à la carte base roulante (moteur); Faire tourner le robot sur lui-même; Appel fini; Passer la carte en mode maintenance; Appel de la fonction mode maintenance; Intégrer la carte moteur/ Appeler la carte moteur; Afficher : "Gyroscope opérationnel"; Fin d'écriture et d'enregistrement; Envoyer les enregistrements à la carte maintenance; Enregistrements envoyés; Afficher : "Gyroscope défaillant"; Fin d'enregistrement; Enregistrer la valeur de R; faire le checksum de toutes les cartes.

"starting Test" valide ET carte en mode maintenance

Action terminée ET valeur de R est envoyée Action terminée ET pas de valeur de retour

NB: Le but de "Starting test" est d'étudier l'état du processeur et de la RAM , càd s'ils sont capables de stocker une variable, de calculer une autre, de les ressortir... De plus, l'objectif de ce test est de savoir si on est capable de

Mise

## Grafcet Mise sous tension (MST)

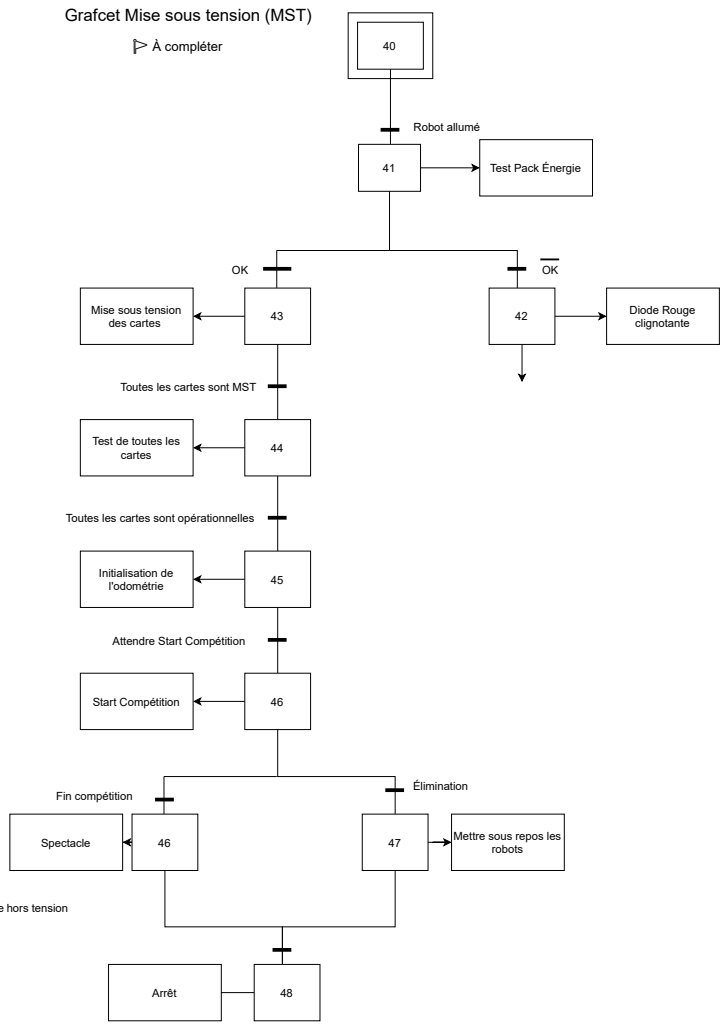
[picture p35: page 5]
Test Pack Énergie; Robot allumé; Diode Rouge clignotante; 45 Initialisation de l'odométrie; Start Compétition; Spectacle; Fin compétition; Élimination; e hors tension; robots 47; Arrêt; 🚩 À compléter

Mise sous tension
des cartes

Toutes les cartes sont MST

Test de toutes les
cartes

Toutes les cartes sont opérationnelles

Attendre Start Compétition

Mettre sous repos les

NB: Le Pi a besoin d'une alimentation en courant continu de 5V la plus propre possible. En pratique, le Pi

## Grafcet alimentation

NB: La STM32 peut être alimentée en 5V par la broche 3 ou l'USB. Elle embarque un régulateur 3.3 V pour
alimenter le processeur. Elle peut être
alimentée entre 2 V et 3.6V par la

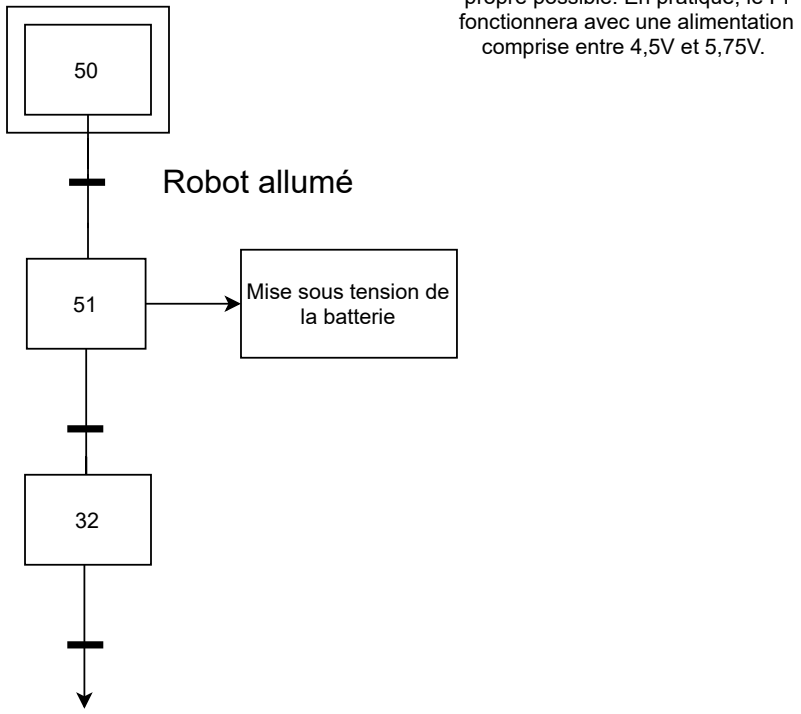
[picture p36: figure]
fonctionnera avec une alimentation comprise entre 4,5V et 5,75V.; Robot allumé; Mise sous tension de la batterie

broche 1. Donc Min = 2V et Max = 5V | 50

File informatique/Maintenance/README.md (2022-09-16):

Dossier contenant les Grafcets et l'IHM de maintenance (en PHP) accompagnée de sa documentation (générée avec PHPDocumentor : https://github.com/phpdocumentor/phpdocumentor | https://docs.phpdoc.org/)

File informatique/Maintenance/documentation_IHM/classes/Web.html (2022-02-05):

# Documentation

Search for

Menu

## Packages

#### Application

## Reports

### Class Diagram

### Deprecated

### Errors

### Markers

## Indices

### Files

- Application

## Web

## in package

## Application

web_class.php : 22

Classe définissant les attributs, accésseurs et méthodes d'un objet de type Web

L'appel et l'utilisation des différents composants de la classe est effectué dans la page index.php

##### Tags

example

$web = new Web("Tableau de bord");

### Table of Contents

$body : string

Le corps de la page web

$head : string

L'en-tête de la page web

$title : string

Le titre de la page web

__construct() : void

Constructeur de la classe Web

addCSSlink() : void

Ajout du lien dans le head vers la page de style

addFooter() : void

Ajout du pied de page au site suivant le thème du site + concaténation avec le body

addIcon() : void

Ajout une icone du site

addJSlink() : void

Ajout du lien dans le head vers la page de java script

addNavBar() : void

Ajout de la barre de navigation

addTile() : string

Ajout d'un bloc de type tuile

addToBody() : void

Setter de l'attribut body

addToHead() : void

Setter de l'attribut head

getBody() : string

Accesseur de l'attribut body

getHead() : string

Accesseur de l'attribut head

getTitle() : string

Accesseur de l'attribut title

toHTML() : string

Ajout de toutes les balises html de la page

### Properties

#### $body

web_class.php : 27

Le corps de la page web

private string $body

#### $head

web_class.php : 24

L'en-tête de la page web

private string $head

#### $title

web_class.php : 30

Le titre de la page web

private string $title

### Methods

#### __construct()

web_class.php : 39

Constructeur de la classe Web

public __construct([string $title = "" ]) : void

Permet d'instancier des objets de type Web

##### Parameters

$title : string = ""

Titre de la page web

##### Return values

void —

#### addCSSlink()

web_class.php : 102

Ajout du lien dans le head vers la page de style

public addCSSlink(string $link) : void

Transforme le lien en balise html et concatene le tout

##### Parameters

$link : string

Lien vers la page de style CSS

##### Return values

void —

#### addFooter()

web_class.php : 137

Ajout du pied de page au site suivant le thème du site + concaténation avec le body

public addFooter([string $color = "dark" ]) : void

##### Parameters

$color : string = "dark"

La couleur de thème du site

##### Tags

example

$web->addFooter($theme);

##### Return values

void —

#### addIcon()

web_class.php : 126

Ajout une icone du site

public addIcon(string $link) : void

Transforme le nom d'image en balise html et concatène le tout

##### Parameters

$link : string

Lien du chemin relatif vers l'image d'illustration de la page web

##### Return values

void —

#### addJSlink()

web_class.php : 114

Ajout du lien dans le head vers la page de java script

public addJSlink(string $link) : void

Transforme le lien en balise html et concatene le tout

##### Parameters

$link : string

Lien vers la page de script JS

##### Return values

void —

#### addNavBar()

web_class.php : 214

Ajout de la barre de navigation

public addNavBar([string $color = "dark" ]) : void

##### Parameters

$color : string = "dark"

Couleur de thème de la page web

##### Tags

example

$web->addNavBar($theme);

##### Return values

void —

#### addTile()

web_class.php : 188

Ajout d'un bloc de type tuile

public addTile(string $color, string $title[, int $margin = 40 ]) : string

##### Parameters

$color : string

La couleur du fond de la tuile

$title : string

Le titre de la tuile

$margin : int = 40

Le nombre, en pixels, du décalage du titre de la tuile vers la droite de l'écran

##### Tags

example

$tile_1 = $web->addTile("primary", "Lancer diagnostic");

##### Return values

string —

$html Le contenu de la page web

#### addToBody()

web_class.php : 91

Setter de l'attribut body

public addToBody(string $body) : void

Concatene l'attribut body

##### Parameters

$body : string

Suite du corps de la page web actuel

##### Tags

example

$web->addToBody("coucou");

##### Return values

void —

#### addToHead()

web_class.php : 79

Setter de l'attribut head

public addToHead(string $head) : void

Concatene l'attribut head

##### Parameters

$head : string

Suite de l'entête de la page web actuelle

##### Return values

void —

#### getBody()

web_class.php : 59

Accesseur de l'attribut body

public getBody() : string

##### Return values

string —

$body Le corps du site

#### getHead()

web_class.php : 50

Accesseur de l'attribut head

public getHead() : string

##### Return values

string —

$head L'en-tête de la page web

#### getTitle()

web_class.php : 68

Accesseur de l'attribut title

public getTitle() : string

##### Return values

string —

$title Le titre du site web

#### toHTML()

web_class.php : 279

Ajout de toutes les balises html de la page

public toHTML([string $color = "dark" ]) : string

##### Parameters

$color : string = "dark"

Couleur de thème de la page web

##### Tags

example

echo $web->toHTML($theme);

##### Return values

string —

$html Le contenu de la page web

## Search results

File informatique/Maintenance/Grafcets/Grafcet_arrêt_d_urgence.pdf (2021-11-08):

Compétition

Actionneur -> Energie 0
Carte info -> Energie
Ecriture fichier log
AU | AU

#Grafcet arrêt d'urgence

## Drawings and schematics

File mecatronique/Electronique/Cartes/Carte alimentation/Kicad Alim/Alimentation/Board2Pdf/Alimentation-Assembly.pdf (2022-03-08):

# canL NC

# 5V NO

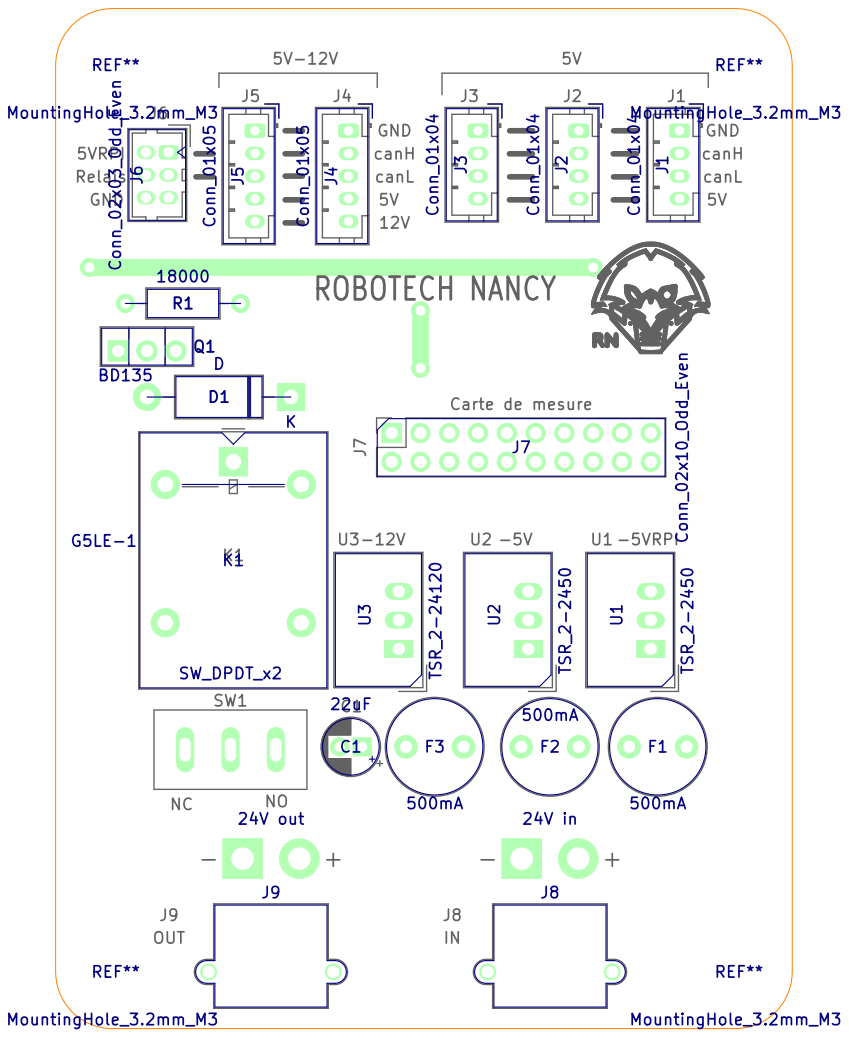
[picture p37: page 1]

1 | 2 | 3 | 4 | 5 | 6

A

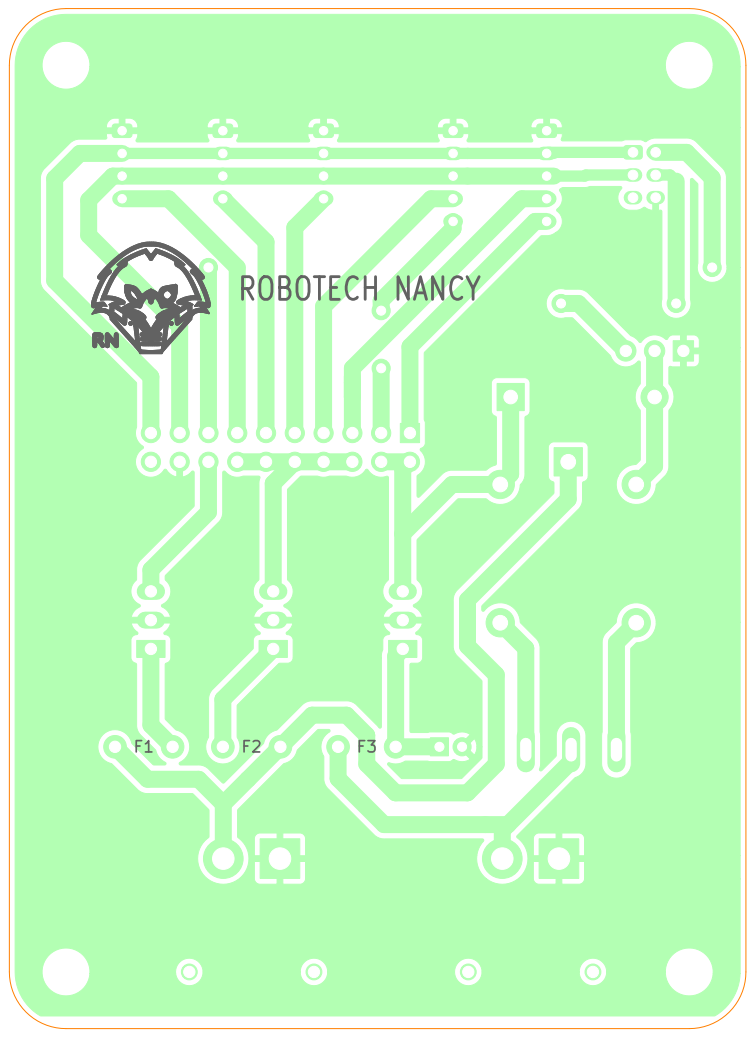
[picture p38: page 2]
ROBOTECH NANCY; D Date: KiCad E.D.A. kicad (6.0.0) Size: A4; Rev:; Id: 1/1 Title:; File: Alimentation.kicad_pcb; Sheet: Assembly

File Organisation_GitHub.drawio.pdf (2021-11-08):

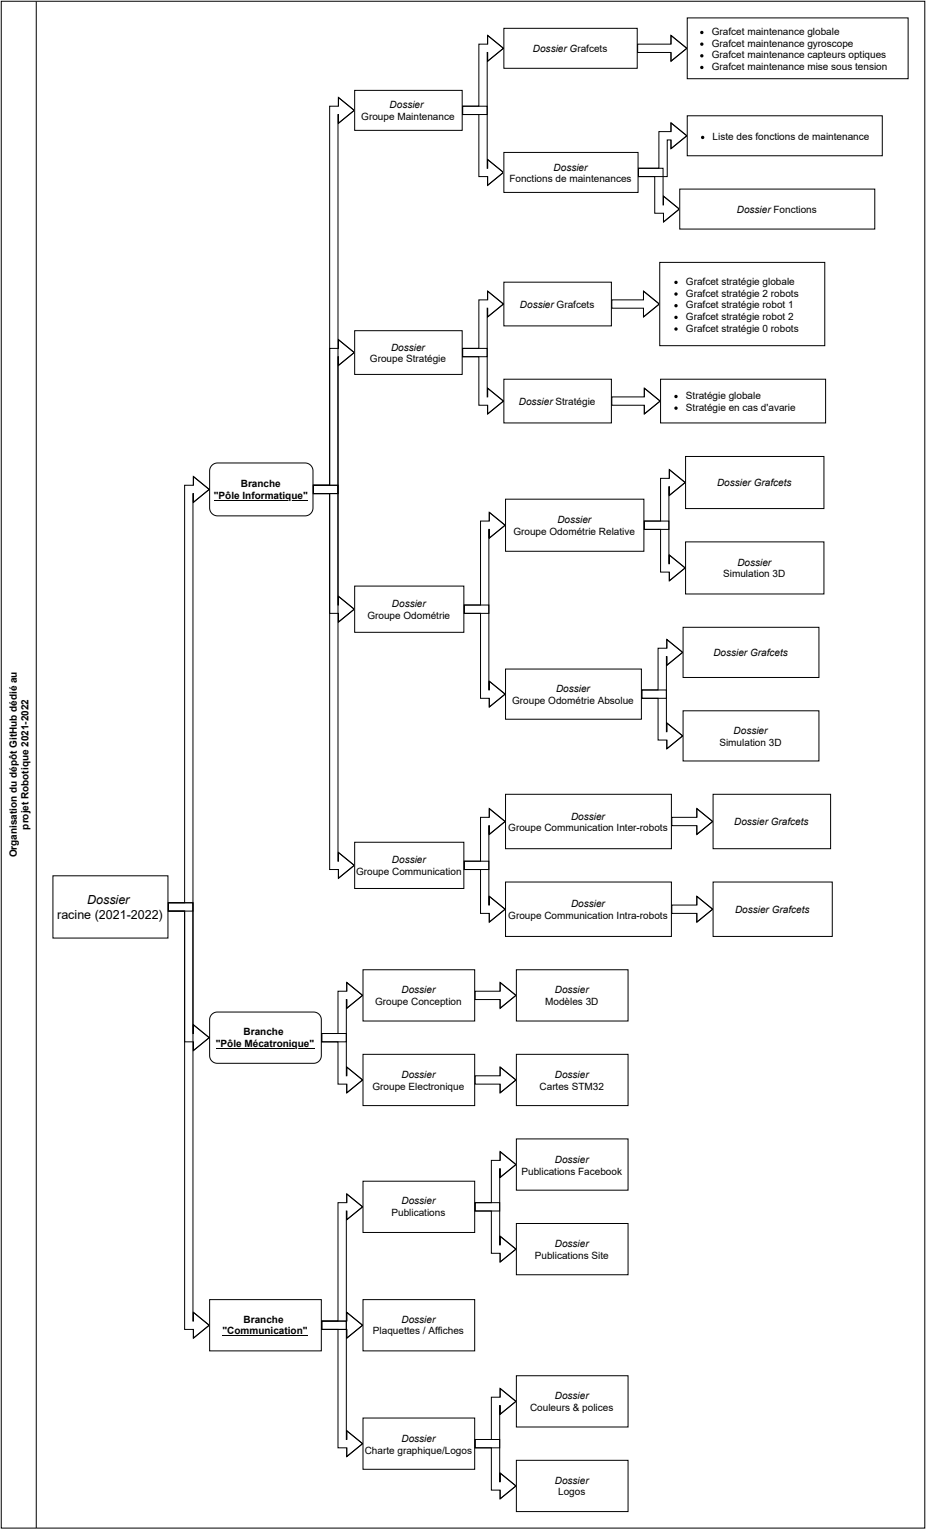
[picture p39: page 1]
projet Robotique 2021-2022; Dossier racine (2021-2022); Branche "Pôle Informatique"; Branche "Pôle Mécatronique"; Dossier Groupe Maintenance; Dossier Groupe Stratégie; Dossier Groupe Odométrie; Dossier Groupe Communication; Dossier; Dossier Groupe Conception; Dossier Groupe Electronique; Branche "Communication"; Dossier Modèles 3D; Dossier Cartes STM32; Dossier Grafcets; Dossier Stratégie; Dossier Publications; Dossier Plaquettes / Affiches; Dossier Publications Facebook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

Grafcet maintenance globale
Grafcet maintenance gyroscope
Grafcet maintenance capteurs optiques
Grafcet maintenance mise sous tension

Liste des fonctions de maintenance

Fonctions de maintenances

Grafcet stratégie globale
Grafcet stratégie 2 robots
Grafcet stratégie robot 1
Grafcet stratégie robot 2
Grafcet stratégie 0 robots

Stratégie globale
Stratégie en cas d'avarie

Groupe Odométrie Relative

Organisation du dépôt GitHub dédié au

Groupe Odométrie Absolue

Groupe Communication Inter-robots

Groupe Communication Intra-robots

Charte graphique/Logos

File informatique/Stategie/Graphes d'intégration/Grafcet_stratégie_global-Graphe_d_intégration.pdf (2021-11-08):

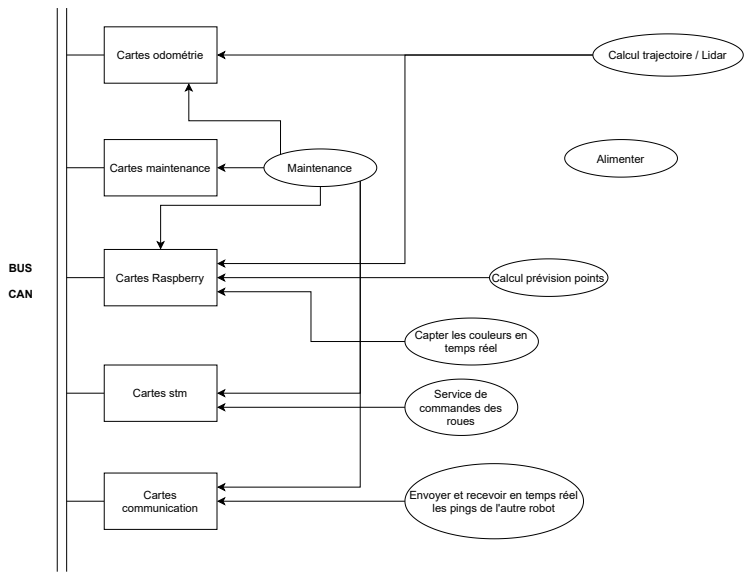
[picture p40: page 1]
BUS; CAN; Cartes odométrie; Cartes maintenance; Cartes communication; Cartes stm; Cartes Raspberry; Maintenance; Service de commandes des roues; Alimenter

Calcul trajectoire / Lidar

Calcul prévision points

Capter les couleurs en
temps réel

Envoyer et recevoir en temps réel
les pings de l'autre robot

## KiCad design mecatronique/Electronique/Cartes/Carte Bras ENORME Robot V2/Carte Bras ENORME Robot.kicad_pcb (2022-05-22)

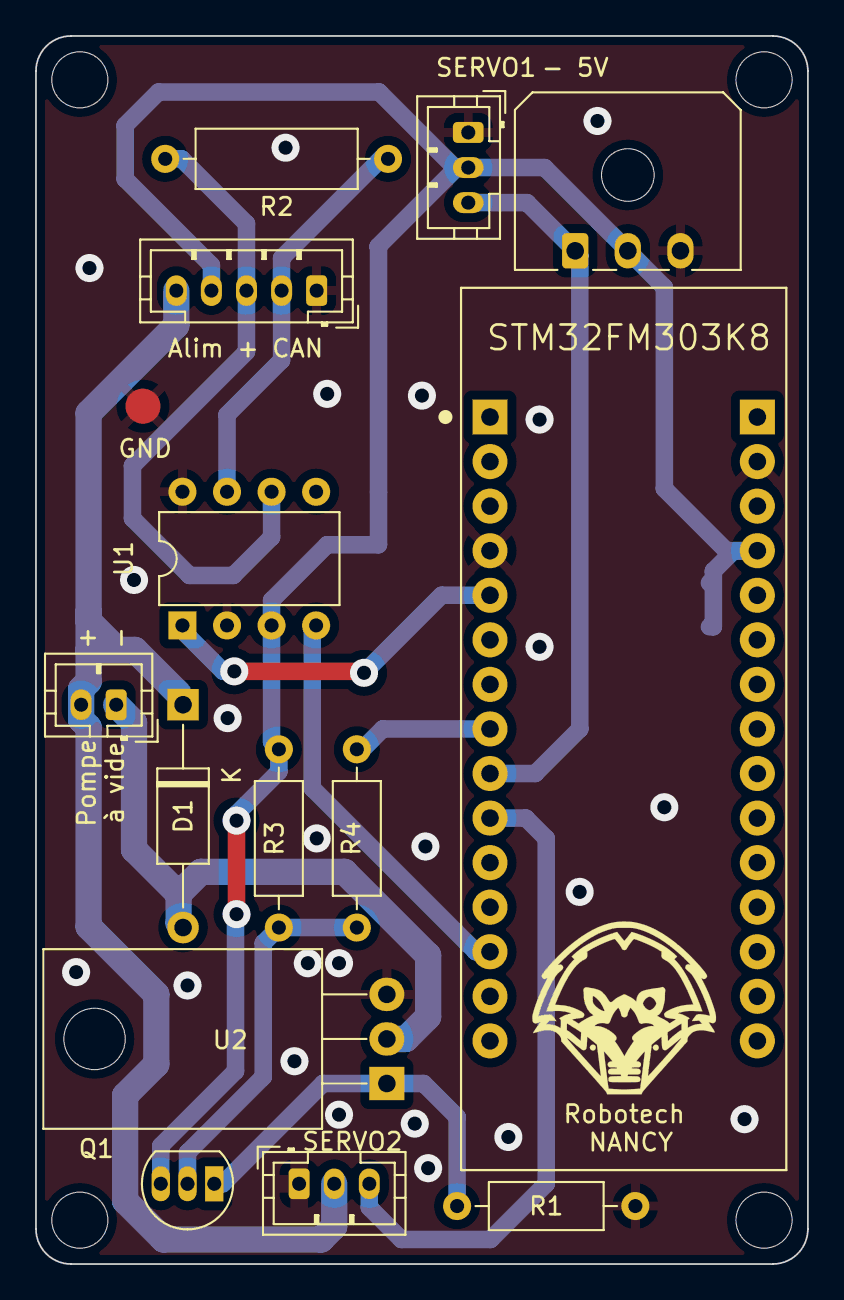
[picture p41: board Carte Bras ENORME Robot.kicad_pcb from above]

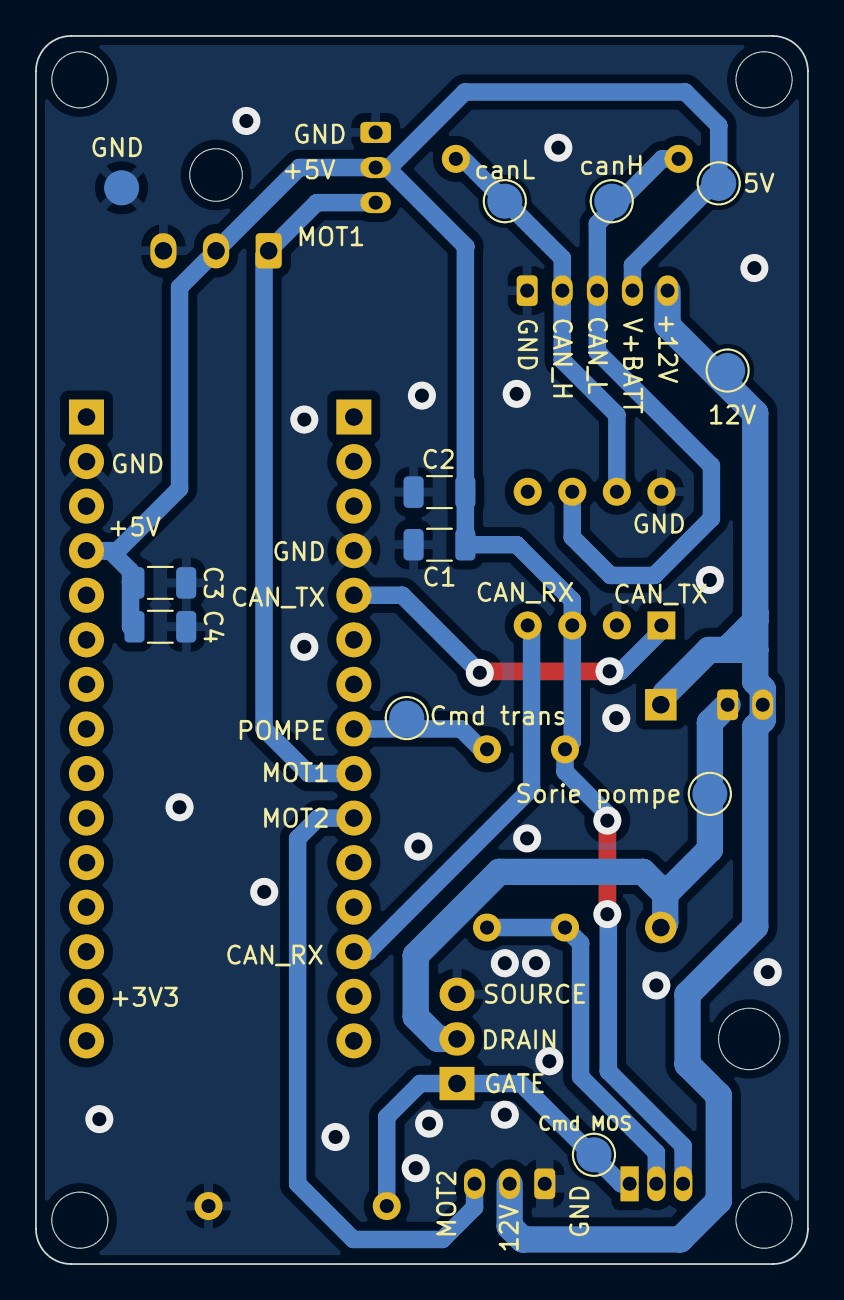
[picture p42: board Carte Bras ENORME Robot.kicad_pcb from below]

Board: 2 copper layers, 44.0 x 70.0 mm, 25 parts (11 on the bottom side), 13 nets.

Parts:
BUS_CAN1: Conn_01x05; JST_PH_B5B-PH-K_1x05_P2.00mm_Vertical
C1, C2, C3, C4: C; C_1206_3216Metric
D1: D; D_A-405_P12.70mm_Horizontal
JS1: Molex_Micro-Fit_3.0_43650-0300_1x03_P3.00mm_Horiz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; Molex_Micro-Fit_3.0_43650-0300_1x03_P3.00mm_Horizontal
PompeAVide1: Conn_01x02; JST_PH_B2B-PH-K_1x02_P2.00mm_Vertical
Q1: BC557; TO-92_Inline
R1: 1k; R_Axial_DIN0207_L6.3mm_D2.5mm_P10.16mm_Horizontal
R2: R; R_Axial_DIN0309_L9.0mm_D3.2mm_P12.70mm_Horizontal
R3: 10k; R_Axial_DIN0207_L6.3mm_D2.5mm_P10.16mm_Horizontal
R4: 180; R_Axial_DIN0207_L6.3mm_D2.5mm_P10.16mm_Horizontal
SERVO1, SERVO2: Conn_01x03; JST_PH_B3B-PH-K_1x03_P2.00mm_Vertical
STM32FM303K8: NUCLEO-F303K8; MODULE_NUCLEO-F303K8
TP2, TP3, TP4, TP5, TP6, TP7, TP8: TestPoint; TestPoint_Pad_D2.0mm
U1: MCP2551-I-P; DIP-8_W7.62mm
U2: IRFZ44NPBF; TO-220-3_Horizontal_TabDown

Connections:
+5V: BUS_CAN1.4, C1.1, C2.1, C3.2, C4.2, JS1.2, Q1.3 (E), R3.1, SERVO1.2, STM32FM303K8.4.4 (+5V), TP3.1, U1.3 (VDD)
+12V: BUS_CAN1.5, D1.1 (K), PompeAVide1.2, SERVO2.2, TP6.1
CAN_H: BUS_CAN1.2, R2.1, TP4.1, U1.7 (CANH)
CAN_L: BUS_CAN1.3, R2.2, TP5.1, U1.6 (CANL)
CAN_RX: STM32FM303K8.3.13 (PA11), U1.4 (RXD)
CAN_TX: STM32FM303K8.3.5 (PA12), U1.1 (TXD)
GND: BUS_CAN1.1, C1.2, C2.2, C3.1, C4.1, JS1.3, R1.2, SERVO1.1, SERVO2.1, STM32FM303K8.3.4 (GND), STM32FM303K8.4.2 (GND), U1.2 (VSS), U1.8 (Rs), U2.3
MOT1: JS1.1, SERVO1.3, STM32FM303K8.3.9 (PB1)
MOT2: SERVO2.3, STM32FM303K8.3.10 (PF0)
unnamed: D1.2 (A), PompeAVide1.1, TP2.1, U2.2
unnamed: Q1.1 (C), R1.1, TP8.1, U2.1
unnamed: Q1.2 (B), R3.2, R4.2
POMPE: R4.1, STM32FM303K8.3.8 (PB6), TP7.1

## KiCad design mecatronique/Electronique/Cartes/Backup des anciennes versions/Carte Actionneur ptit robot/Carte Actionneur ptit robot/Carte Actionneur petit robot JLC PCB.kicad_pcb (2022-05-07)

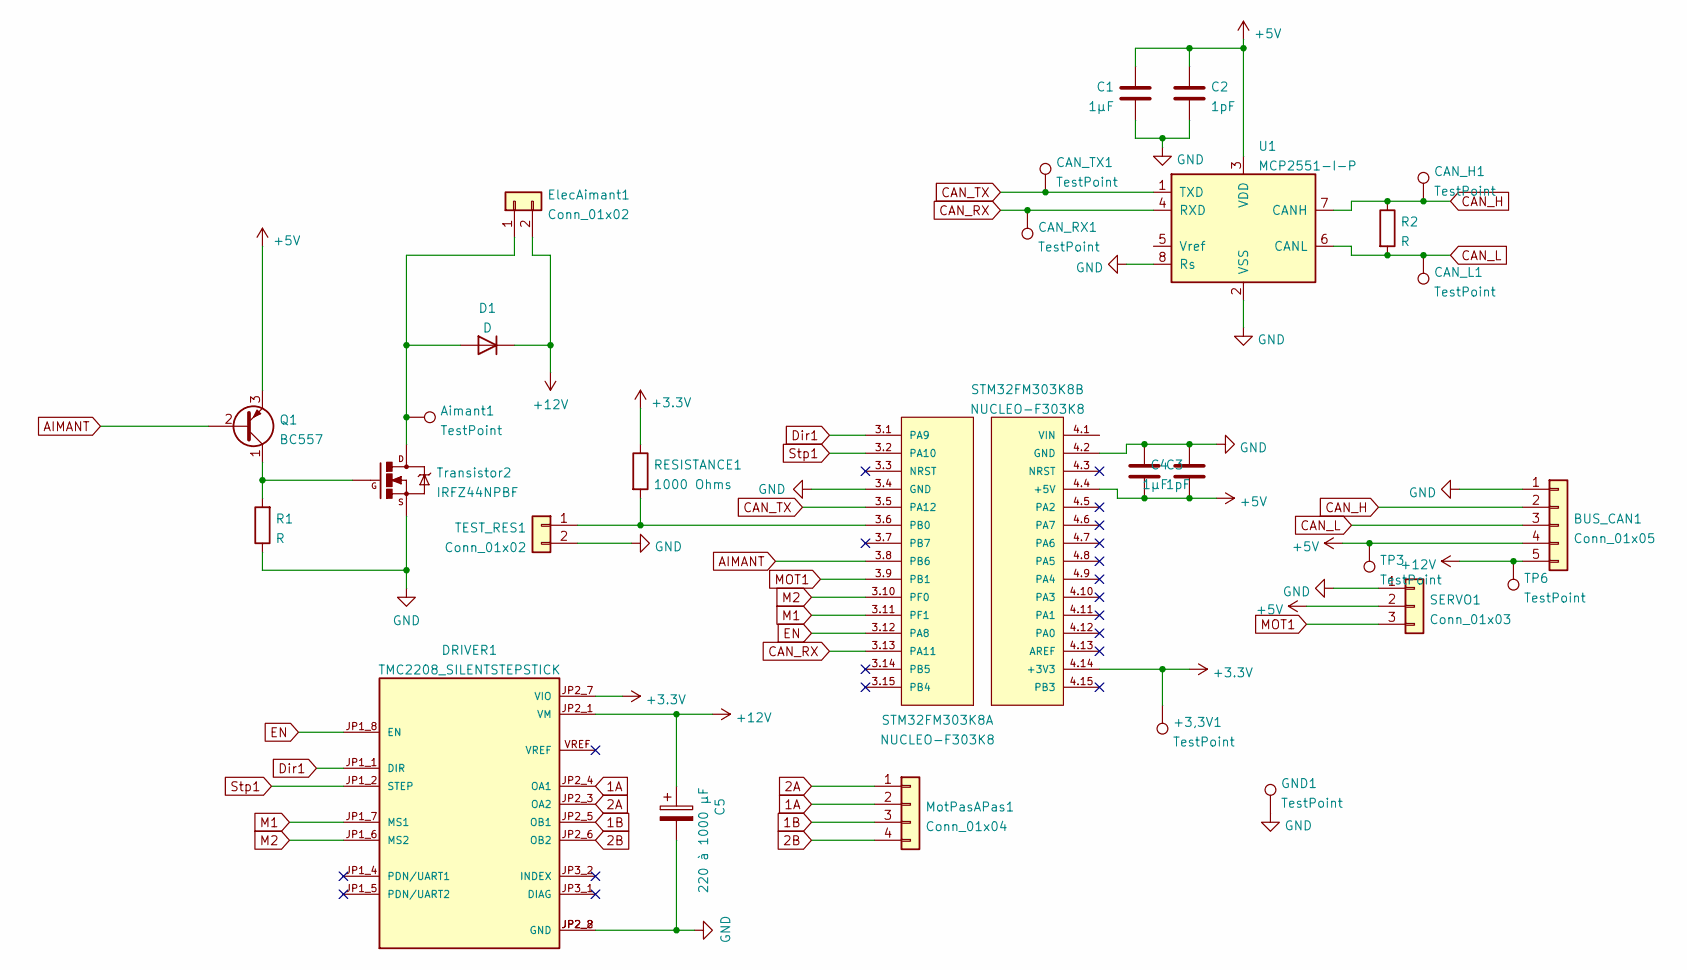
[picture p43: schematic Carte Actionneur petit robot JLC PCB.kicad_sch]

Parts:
+3,3V1: TestPoint; TestPoint_Pad_D2.0mm
Aimant1: TestPoint; TestPoint_Pad_D2.0mm
BUS_CAN1: Conn_01x05; JST_PH_B5B-PH-K_1x05_P2.00mm_Vertical
C1, C4: 1µF; C_1206_3216Metric
C2, C3: 1pF; C_1206_3216Metric
C5: 220 à 1000 µF; C_Elec_8x10.2
CAN_H1: TestPoint; TestPoint_Pad_D2.0mm
CAN_L1: TestPoint; TestPoint_Pad_D2.0mm
CAN_RX1: TestPoint; TestPoint_Pad_D2.0mm
CAN_TX1: TestPoint; TestPoint_Pad_D2.0mm
D1: D; D_A-405_P12.70mm_Horizontal
DRIVER1: TMC2208_SILENTSTEPSTICK; MODULE_TMC2208_SILENTSTEPSTICK
ElecAimant1: Conn_01x02; JST_PH_B2B-PH-K_1x02_P2.00mm_Vertical
GND1: TestPoint; TestPoint_Pad_D2.0mm
MotPasAPas1: Conn_01x04; PinSocket_1x04_P2.54mm_Vertical
Q1: BC557; TO-92_Inline
R1: R; R_Axial_DIN0207_L6.3mm_D2.5mm_P15.24mm_Horizontal
R2: R; R_Axial_DIN0309_L9.0mm_D3.2mm_P12.70mm_Horizontal
RESISTANCE1: 1000 Ohms; R_Axial_DIN0207_L6.3mm_D2.5mm_P15.24mm_Horizontal
SERVO1: Conn_01x03; JST_PH_B3B-PH-K_1x03_P2.00mm_Vertical
STM32FM303K8: NUCLEO-F303K8; iou; PARTREV 3
TEST_RES1: Conn_01x02; PinSocket_1x02_P2.54mm_Vertical
TP3, TP6: TestPoint; TestPoint_Pad_D2.0mm
Transistor2: IRFZ44NPBF; TO-220-3_Horizontal_TabDown
U1: MCP2551-I-P; DIP-8_W7.62mm

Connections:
1A: DRIVER1.JP2_4 (OA1), MotPasAPas1.2
1B: DRIVER1.JP2_5 (OB1), MotPasAPas1.3
2A: DRIVER1.JP2_3 (OA2), MotPasAPas1.1
2B: DRIVER1.JP2_6 (OB2), MotPasAPas1.4
+3V3: +3,3V1.1, DRIVER1.JP2_7 (VIO), RESISTANCE1.1, STM32FM303K8.4.14 (+3V3)
+5V: BUS_CAN1.4, C1.1, C2.1, C3.2, C4.2, Q1.3 (E), SERVO1.2, STM32FM303K8.4.4 (+5V), TP3.1, U1.3 (VDD)
+12V: BUS_CAN1.5, C5.1, D1.1 (K), DRIVER1.JP2_1 (VM), ElecAimant1.2, TP6.1
AIMANT: Q1.2 (B), STM32FM303K8.3.8 (PB6)
CAN_H: BUS_CAN1.2, CAN_H1.1, R2.1, U1.7 (CANH)
CAN_L: BUS_CAN1.3, CAN_L1.1, R2.2, U1.6 (CANL)
CAN_RX: CAN_RX1.1, STM32FM303K8.3.13 (PA11), U1.4 (RXD)
CAN_TX: CAN_TX1.1, STM32FM303K8.3.5 (PA12), U1.1 (TXD)
Dir1: DRIVER1.JP1_1 (DIR), STM32FM303K8.3.1 (PA9)
EN: DRIVER1.JP1_8 (EN), STM32FM303K8.3.12 (PA8)
GND: BUS_CAN1.1, C1.2, C2.2, C3.1, C4.1, C5.2, DRIVER1.JP2_2 (GND), DRIVER1.JP2_8 (GND), GND1.1, R1.1, SERVO1.1, STM32FM303K8.3.4 (GND), STM32FM303K8.4.2 (GND), TEST_RES1.2, Transistor2.3, U1.2 (VSS), U1.8 (Rs)
M1: DRIVER1.JP1_7 (MS1), STM32FM303K8.3.11 (PF1)
M2: DRIVER1.JP1_6 (MS2), STM32FM303K8.3.10 (PF0)
MOT1: SERVO1.3, STM32FM303K8.3.9 (PB1)
unnamed: Aimant1.1, D1.2 (A), ElecAimant1.1, Transistor2.2
unnamed: Q1.1 (C), R1.2, Transistor2.1
unnamed: RESISTANCE1.2, STM32FM303K8.3.6 (PB0), TEST_RES1.1
Stp1: DRIVER1.JP1_2 (STEP), STM32FM303K8.3.2 (PA10)

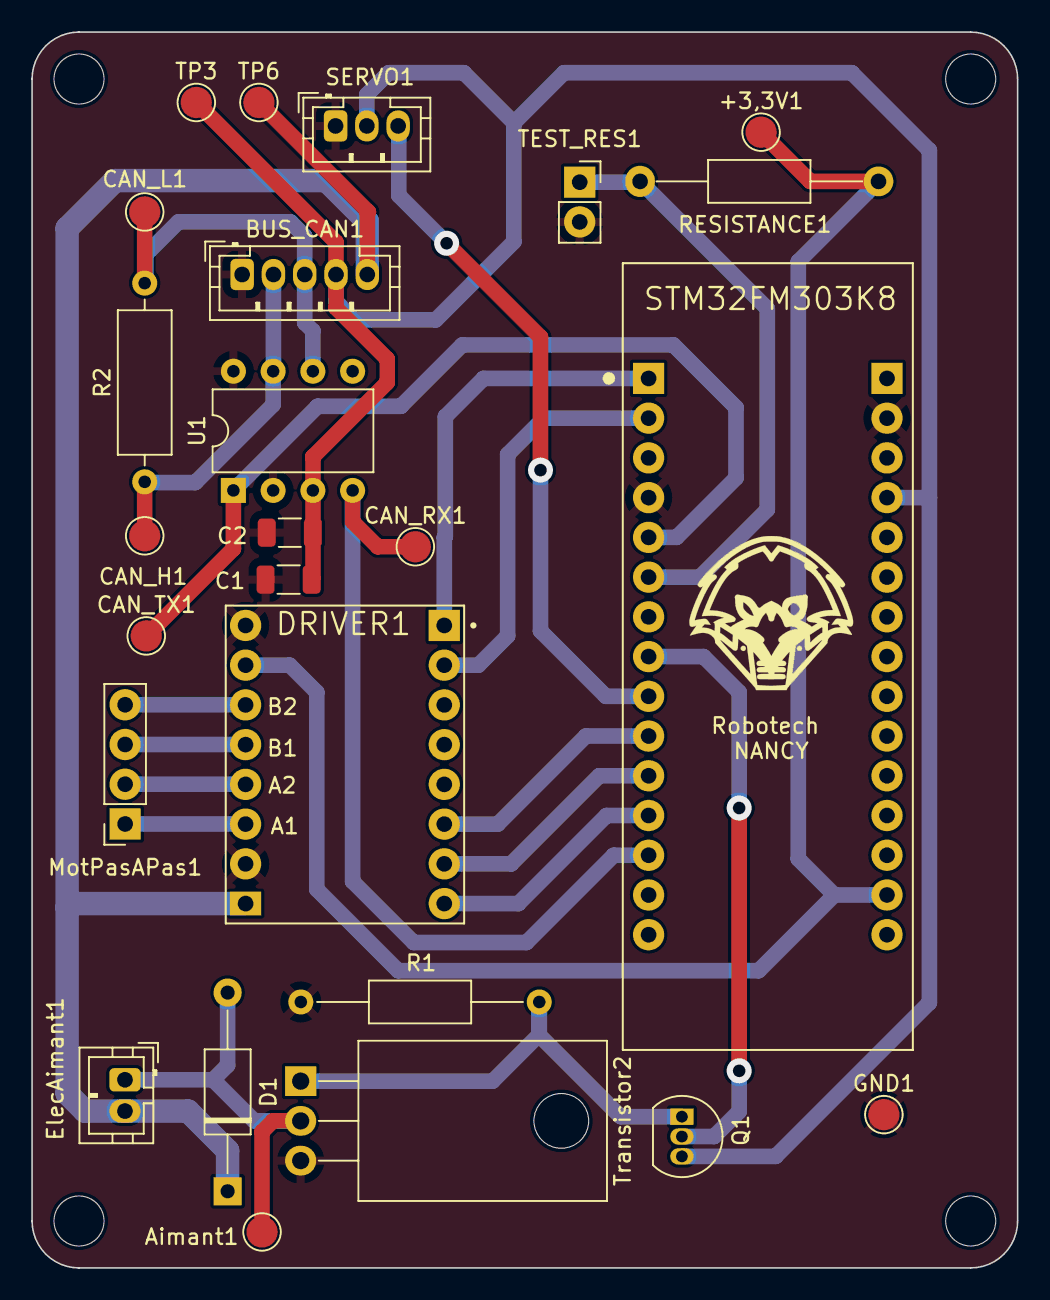
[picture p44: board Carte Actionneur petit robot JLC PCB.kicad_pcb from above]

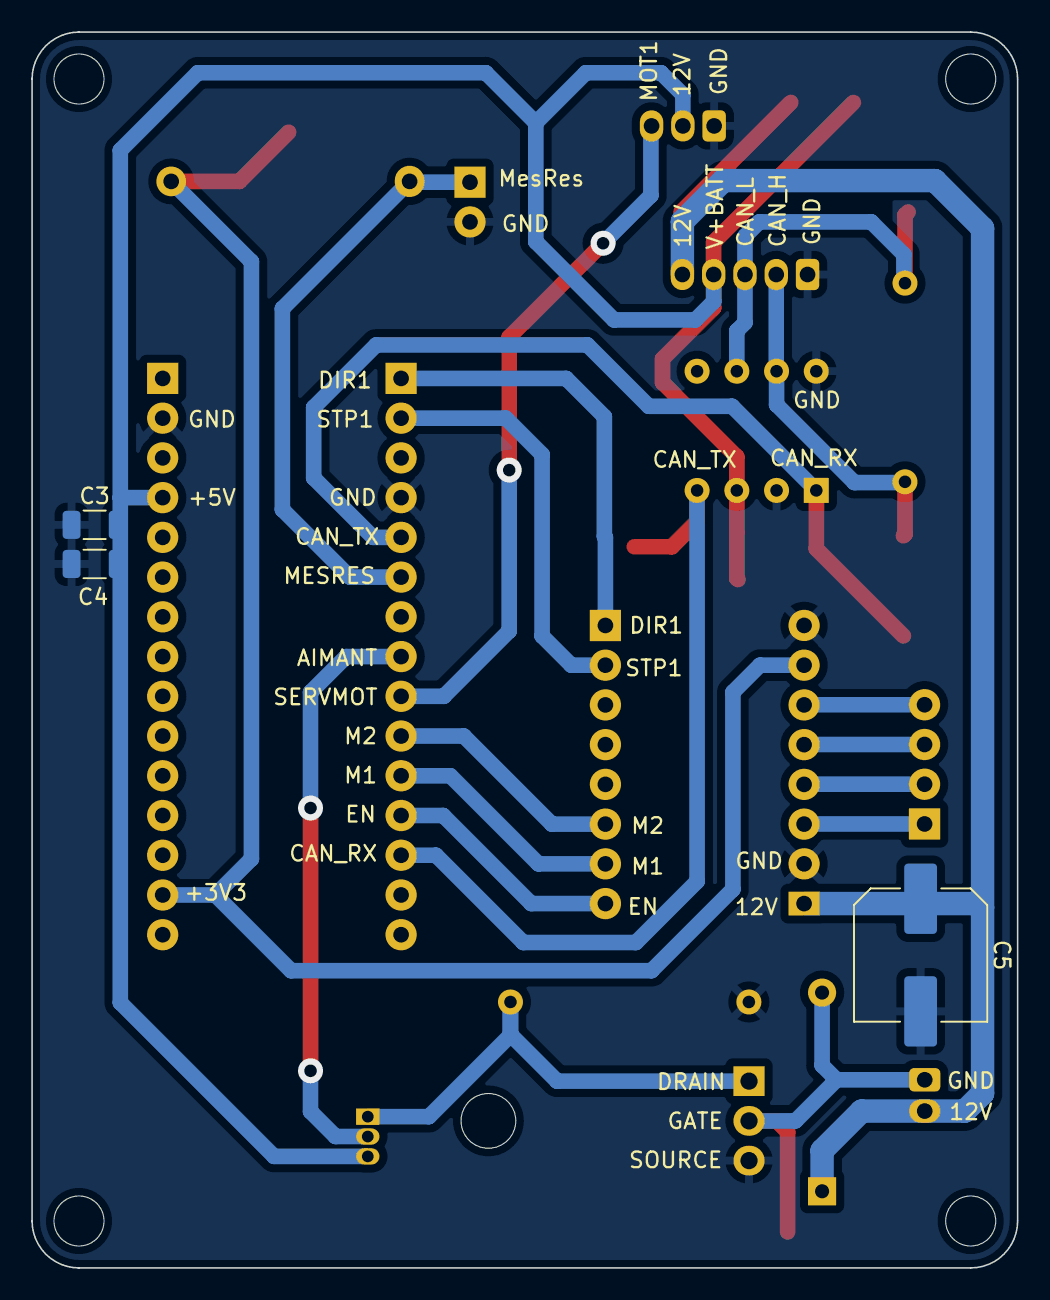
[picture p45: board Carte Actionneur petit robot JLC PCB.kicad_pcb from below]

Board: 2 copper layers, 63.0 x 79.0 mm, 28 parts (3 on the bottom side), 22 nets.

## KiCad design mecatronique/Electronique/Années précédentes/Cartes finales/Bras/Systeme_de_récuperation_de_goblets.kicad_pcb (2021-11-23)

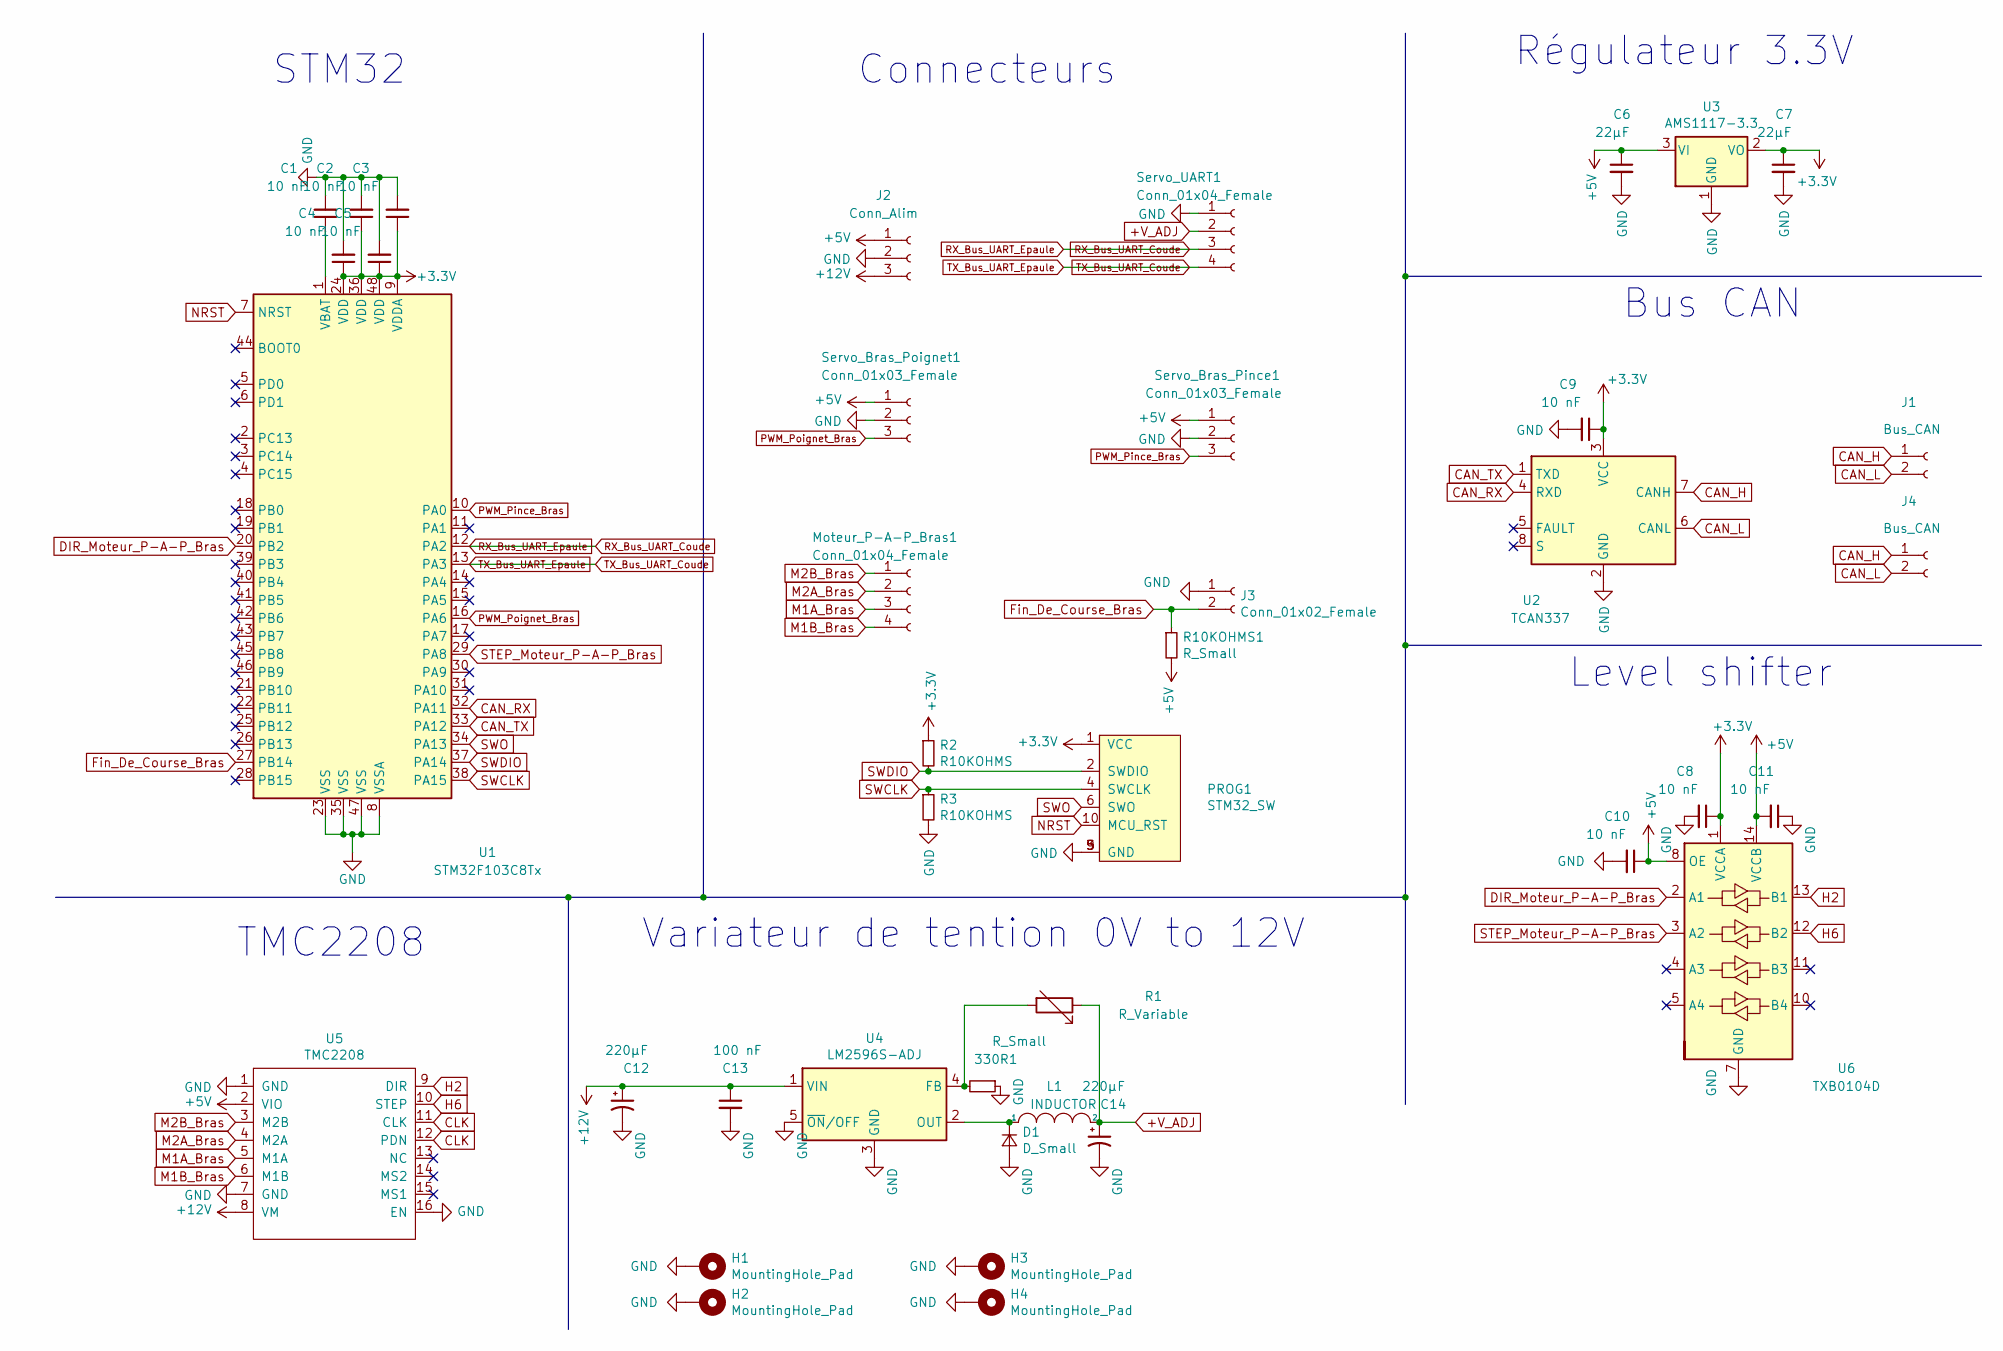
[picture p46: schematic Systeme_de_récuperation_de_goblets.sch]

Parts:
330R1: R_Small; R_0603_1608Metric; MFR.Part # 0603WAF3300T5E; LCSC Part # C23138
C1, C2, C3, C4, C5, C8, C9, C10, C11: 10 nF; C_0402_1005Metric; MFR.Part # CL05B103KB5NNNC; LCSC Part # C15195
C6, C7: 22µF; C_0402_1005Metric; MFR.Part # 0402B223K500NT; LCSC Part # C1532
C12, C14: 220µF; CP_Elec_10x10; MFR.Part # VEJ221M1HTR-1010; LCSC Part # C176670
C13: 100 nF; C_0402_1005Metric; MFR.Part # CC0603KRX7R9BB104; LCSC Part # C14664
D1: D_Small; D_SMA; MFR.Part # ES2AA-13-F; LCSC Part # C151575
H1, H2, H3, H4: MountingHole_Pad; MountingHole_3.2mm_M3_Pad_Via
J1, J4: Bus_CAN; Molex_Nano-Fit_105313-xx02_1x02_P2.50mm_Horizontal
J2: Conn_Alim; Molex_Nano-Fit_105313-xx03_1x03_P2.50mm_Horizontal
J3: Conn_01x02_Female; JST_EH_B2B-EH-A_1x02_P2.50mm_Vertical
L1: INDUCTOR; L_1210_3225Metric
Moteur_P-A-P_Bras1: Conn_01x04_Female; JST_EH_S4B-EH_1x04_P2.50mm_Horizontal
PROG1: STM32_SW; JTAG10
R1: R_Variable; Potentiometer_Bourns_3386C_Horizontal
R2, R3: R10KOHMS; R_0603_1608Metric; MFR.Part# 0603WAF1002T5E; LCSC.Part# C25804
R10KOHMS1: R_Small; R_0603_1608Metric; MFR.Part # 0603WAF1002T5E; LCSC Part # C25804
Servo_Bras_Pince1: Conn_01x03_Female; JST_EH_S3B-EH_1x03_P2.50mm_Horizontal
Servo_Bras_Poignet1: Conn_01x03_Female; JST_EH_S3B-EH_1x03_P2.50mm_Horizontal
Servo_UART1: Conn_01x04_Female; JST_EH_S4B-EH_1x04_P2.50mm_Horizontal
U1: STM32F103C8Tx; LQFP-48_7x7mm_P0.5mm; MFR.Part # STM32F091RCT6; LCSC Part # C89056
U2: TCAN337; SOIC-8-1EP_3.9x4.9mm_P1.27mm_EP2.29x3mm; MFR.Part # TCAN337GDR; LCSC Part # C191004
U3: AMS1117-3.3; SOT-223
U4: LM2596S-ADJ; TO-263-5_TabPin3; MFR.Part # LM2596SX-ADJ/NOPB; LCSC Part # C29781
U5: TMC2208; MFR.Part # TMC2208-LA-T; LCSC Part # C115944
U6: TXB0104D; SOIC-14_3.9x8.7mm_P1.27mm; MFR.Part # TXB0104PWR; LCSC Part # C60708

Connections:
+3V3: C2.1, C3.1, C4.1, C5.1, C7.1, C8.1, C9.1, PROG1.1 (VCC), R2.1, U1.9 (VDDA), U1.24 (VDD), U1.36 (VDD), U1.48 (VDD), U2.3 (VCC), U3.2 (VO), U6.1 (VCCA)
+5V: C6.1, C10.1, C11.2, J2.1, R10KOHMS1.2, Servo_Bras_Pince1.1, Servo_Bras_Poignet1.1, U3.3 (VI), U5.2 (VIO), U6.8 (OE), U6.14 (VCCB)
+12V: C12.1, C13.1, J2.3, U4.1 (VIN), U5.8 (VM)
+V_ADJ: C14.1, L1.2, R1.1, Servo_UART1.2
CAN_H: J1.1, J4.1, U2.7 (CANH)
CAN_L: J1.2, J4.2, U2.6 (CANL)
CAN_RX: U1.32 (PA11), U2.4 (RXD)
CAN_TX: U1.33 (PA12), U2.1 (TXD)
CLK: U5.11 (CLK), U5.12 (PDN)
DIR_Moteur_P-A-P_Bras: U1.20 (PB2), U6.2 (A1)
Fin_De_Course_Bras: J3.2, R10KOHMS1.1, U1.27 (PB14)
GND: 330R1.1, C1.2, C2.2, C3.2, C4.2, C5.2, C6.2, C7.2, C8.2, C9.2, C10.2, C11.1, C12.2, C13.2, C14.2, D1.2 (A), H1.1, H2.1, H3.1, H4.1, J2.2, J3.1, PROG1.3 (GND), PROG1.5 (GND), PROG1.9 (GND), R3.2, Servo_Bras_Pince1.2, Servo_Bras_Poignet1.2, Servo_UART1.1, U1.8 (VSSA), U1.23 (VSS), U1.35 (VSS), U1.47 (VSS), U2.2 (GND), U3.1 (GND), U4.3 (GND), U4.5 (~ON~/OFF), U5.1 (GND), U5.7 (GND), U5.16 (EN), U6.7 (GND)
H2: U5.9 (DIR), U6.13 (B1)
H6: U5.10 (STEP), U6.12 (B2)
M1A_Bras: Moteur_P-A-P_Bras1.3, U5.5 (M1A)
M1B_Bras: Moteur_P-A-P_Bras1.4, U5.6 (M1B)
M2A_Bras: Moteur_P-A-P_Bras1.2, U5.4 (M2A)
M2B_Bras: Moteur_P-A-P_Bras1.1, U5.3 (M2B)
NRST: PROG1.10 (MCU_RST), U1.7 (NRST)
unnamed: 330R1.2, R1.2, U4.4 (FB)
unnamed: C1.1, U1.1 (VBAT)
unnamed: D1.1 (K), L1.1, U4.2 (OUT)
PWM_Pince_Bras: Servo_Bras_Pince1.3, U1.10 (PA0)
PWM_Poignet_Bras: Servo_Bras_Poignet1.3, U1.16 (PA6)
RX_Bus_UART_Coude: Servo_UART1.3, U1.12 (PA2)
STEP_Moteur_P-A-P_Bras: U1.29 (PA8), U6.3 (A2)
SWCLK: PROG1.4 (SWCLK), R3.1, U1.38 (PA15)
SWDIO: PROG1.2 (SWDIO), R2.2, U1.37 (PA14)
SWO: PROG1.6 (SWO), U1.34 (PA13)
TX_Bus_UART_Coude: Servo_UART1.4, U1.13 (PA3)

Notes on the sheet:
Variateur de tention 0V to 12V
TMC2208
Level shifter
STM32
Connecteurs
Bus CAN
Régulateur 3.3V

Board: 2 copper layers, 40 parts (0 on the bottom side), 30 nets, no tracks yet.

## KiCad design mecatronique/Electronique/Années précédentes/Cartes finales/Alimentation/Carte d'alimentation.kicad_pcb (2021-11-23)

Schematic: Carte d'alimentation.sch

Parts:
ACS712xLCTR-20A1: ACS712xLCTR-20A; SOIC-8_3.9x4.9mm_P1.27mm
Batterie1: Batterie; Molex_Micro-Fit_3.0_43045-0412_2x02_P3.00mm_Vertical
C1, C2, C3, C6, C7: 10µF; CP_EIA-3216-10_Kemet-I
C4: 1µF; CP_EIA-3216-10_Kemet-I
C5, C8, C9, C10, C12, C13, C15: 1nF; C_0402_1005Metric
CAN1, CAN2: sortie CAN; Molex_SPOX_5268-02A_1x02_P2.50mm_Horizontal
D2, D3: D_Zener; D_SOD-523; LCSC PART # C455026
H1, H2, H3, H4: MountingHole_Pad; MountingHole_3.2mm_M3_Pad
K1, K2: G5LE-1; Relay_SPDT_Omron-G5LE-1
MOS1, MOS2: 2N7002; SOT-23; LCSC PART # C8545
Moteur1: Moteur; Molex_Micro-Fit_3.0_43045-0612_2x03_P3.00mm_Vertical
PROG1: STM32_SW; JTAG10
R2: 90k; R_0603_1608Metric
R4, R5: 0.035; R_2512_6332Metric; LCSC PART # C87220
R6, R7: 10k; R_0603_1608Metric
R8: 56k; R_0603_1608Metric
R10, R11: 20k; R_0603_1608Metric
RG2: 1150; R_0603_1608Metric; LCSC PART # C22863
RG3: 560; R_0603_1608Metric; LCSC PART # C23204
STM32: STM32F103C8Tx; LQFP-48_7x7mm_P0.5mm
Sortie5V1, Sortie5V2, Sortie5V3, Sortie5V4, Sortie5V6: Sortie 5V; Molex_Nano-Fit_105309-xx02_1x02_P2.50mm_Vertical
Sortiemixte1, Sortiemixte2, Sortiemixte3, Sortiemixte4: Sortie mixte; Molex_Nano-Fit_105309-xx03_1x03_P2.50mm_Vertical
TCAN337: TCAN337; SOIC-8_3.9x4.9mm_P1.27mm
TSR_1-2450: TSR_1-2450; Converter_DCDC_TRACO_TSR-1_THT
TSR_2-2450: TSR_2-2450; Converter_DCDC_TRACO_TSR-1_THT
TSR_2-24120: TSR_2-24120; Converter_DCDC_TRACO_TSR-1_THT
U1: LM1117-3.3; SOT-223; LCSC PART # C126027
U2: ICL7660; SOIC-8_3.9x4.9mm_P1.27mm
U10, U11: AD620; SOIC-8_3.9x4.9mm_P1.27mm
pullDown1: 1k; R_0603_1608Metric
pullUp1: 1k; R_0603_1608Metric

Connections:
3.3V: C4.1, C7.2, C8.2, C10.2, C12.2, C13.2, C15.2, PROG1.1 (VCC), STM32.9, STM32.24, STM32.36, STM32.48, TCAN337.3, U1.2, pullUp1.1
5VDCRasPi: Sortie5V6.1, TSR_2-2450.3
+5V: ACS712xLCTR-20A1.8, C6.1, C9.1, K1.2, K2.5, Moteur1.1, R7.1, Sortie5V1.1, Sortie5V2.1, Sortie5V3.1, Sortie5V4.1, Sortiemixte1.1, Sortiemixte2.1, Sortiemixte3.1, Sortiemixte4.1, TSR_1-2450.3, U1.3, U2.8, U10.7, U11.7
+12V: R8.1, Sortiemixte1.3, Sortiemixte2.3, Sortiemixte3.3, Sortiemixte4.3, TSR_2-24120.3
-5V: C2.1, U2.5, U10.4, U11.4
/AD5_N: R5.1, TSR_1-2450.1, U11.2
/AD12_N: R4.1, TSR_2-24120.1, U10.2
/AD12_P: K2.4, R4.2, U10.3
GND: ACS712xLCTR-20A1.5, Batterie1.3, Batterie1.4, C2.2, C3.2, C4.2, C5.1, C6.2, C7.1, C8.1, C9.2, C10.1, C12.1, C13.1, C15.1, D2.2, D3.2, H1.1, H2.1, H3.1, H4.1, MOS1.2, MOS2.2, Moteur1.4, Moteur1.5, Moteur1.6, PROG1.3 (GND), PROG1.5 (GND), PROG1.9 (GND), R6.2, R10.2, R11.2, STM32.8, STM32.23, STM32.35, STM32.47, Sortie5V1.2, Sortie5V2.2, Sortie5V3.2, Sortie5V4.2, Sortie5V6.2, Sortiemixte1.2, Sortiemixte2.2, Sortiemixte3.2, Sortiemixte4.2, TCAN337.2, TSR_1-2450.2, TSR_2-2450.2, TSR_2-24120.2, U1.1, U2.3, U10.5, U11.5, pullDown1.1
I_5VDC: D3.1, STM32.14, U11.6
I_12VDC: D2.1, STM32.15, U10.6
I_VBatt: ACS712xLCTR-20A1.7, STM32.10
Mes_5VDC: R7.2, R10.1, STM32.19
Mes_12VDC: R8.2, R11.1, STM32.13
Mes_VBatt: R2.2, R6.1, STM32.11
NRST: PROG1.10 (MCU_RST), STM32.7
unnamed: ACS712xLCTR-20A1.1, ACS712xLCTR-20A1.2, K1.4
unnamed: ACS712xLCTR-20A1.6, C5.2
unnamed: C1.1, U2.2
unnamed: C1.2, U2.4
unnamed: C3.1, U2.7
unnamed: K1.5, MOS1.3
unnamed: K2.2, MOS2.3
unnamed: RG2.1, U10.1
unnamed: RG2.2, U10.8
unnamed: RG3.1, U11.1
unnamed: RG3.2, U11.8
Out_VBatt: ACS712xLCTR-20A1.3, ACS712xLCTR-20A1.4, Moteur1.2, Moteur1.3
Relay_12V: MOS2.1, STM32.21
Relay_VBatt: MOS1.1, STM32.22
Rx: STM32.32, TCAN337.4
SWCLK: PROG1.4 (SWCLK), STM32.37, pullDown1.2
SWDIO: PROG1.2 (SWDIO), STM32.34, pullUp1.2
SWO: PROG1.6 (SWO), STM32.38
Tx: STM32.33, TCAN337.1
VBatt: Batterie1.1, Batterie1.2, K1.1, K2.1, R2.1, R5.2, TSR_2-2450.1, U11.3
can_N: CAN1.2, CAN2.2, TCAN337.6
can_P: CAN1.1, CAN2.1, TCAN337.7

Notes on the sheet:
Interface de programmation
Fixation
STM32
CAN
LABEL
Entrées; Sorties
Other needs
Rail 5V
Rail 12V
Rail VBatt

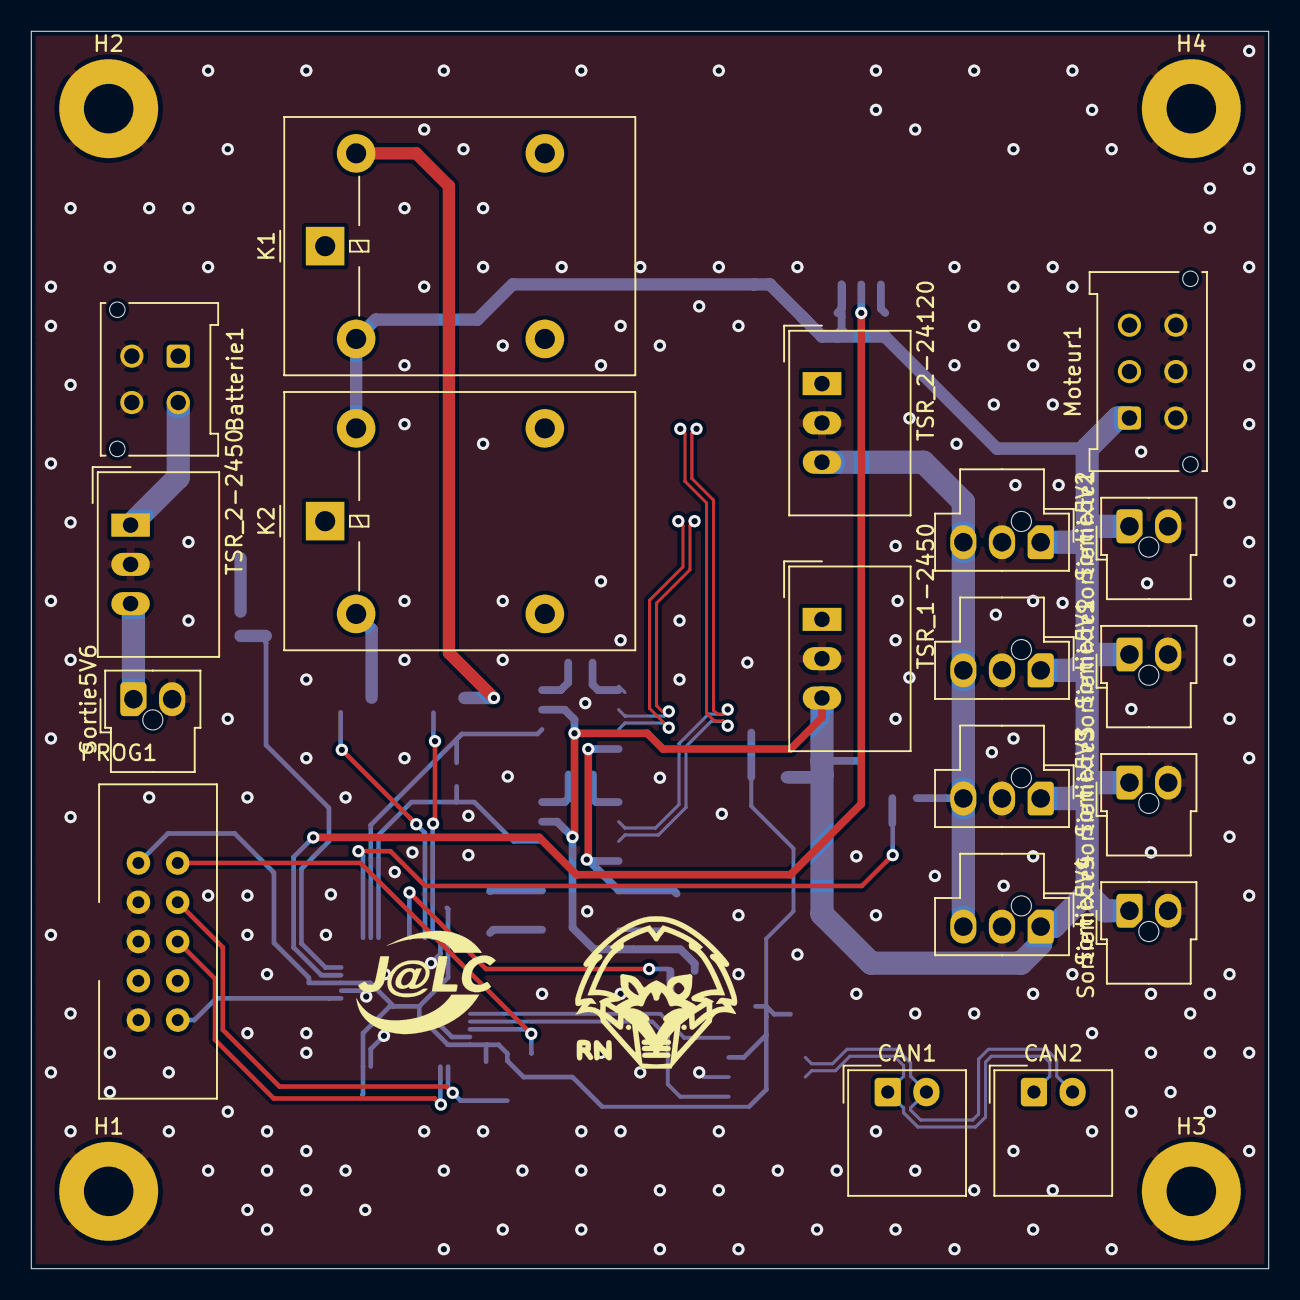
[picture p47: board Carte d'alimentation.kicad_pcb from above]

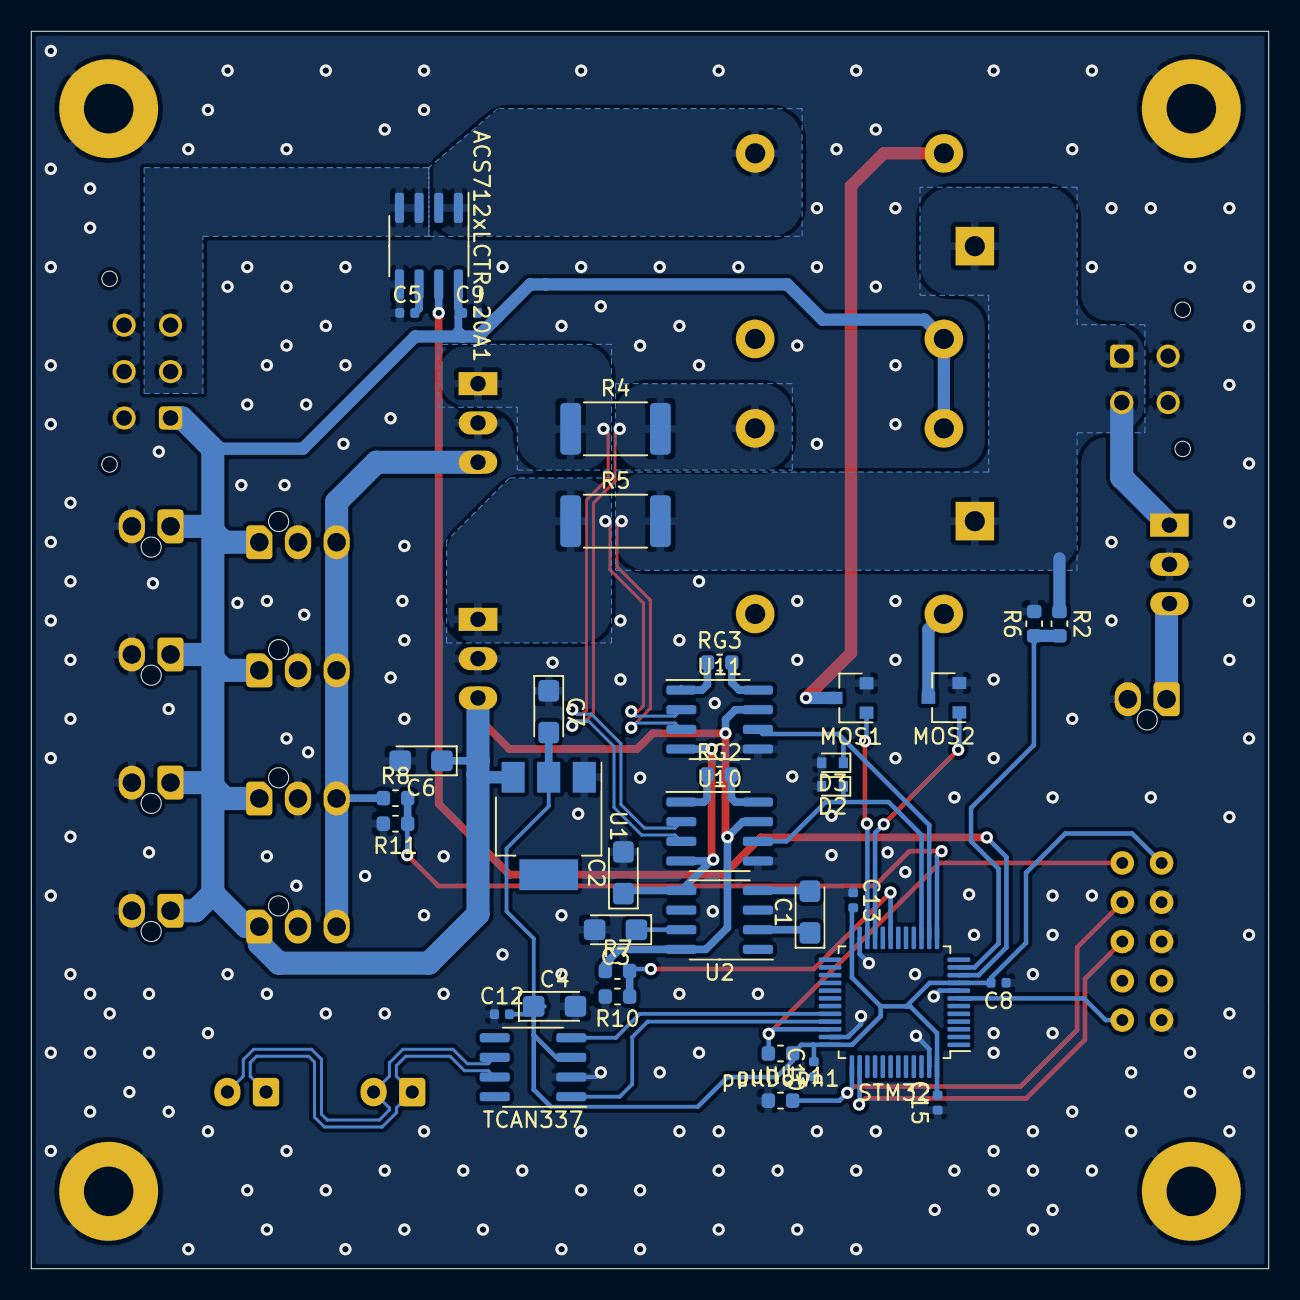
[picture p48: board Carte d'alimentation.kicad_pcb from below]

Board: 2 copper layers, 80.0 x 80.0 mm, 59 parts (36 on the bottom side), 38 nets.

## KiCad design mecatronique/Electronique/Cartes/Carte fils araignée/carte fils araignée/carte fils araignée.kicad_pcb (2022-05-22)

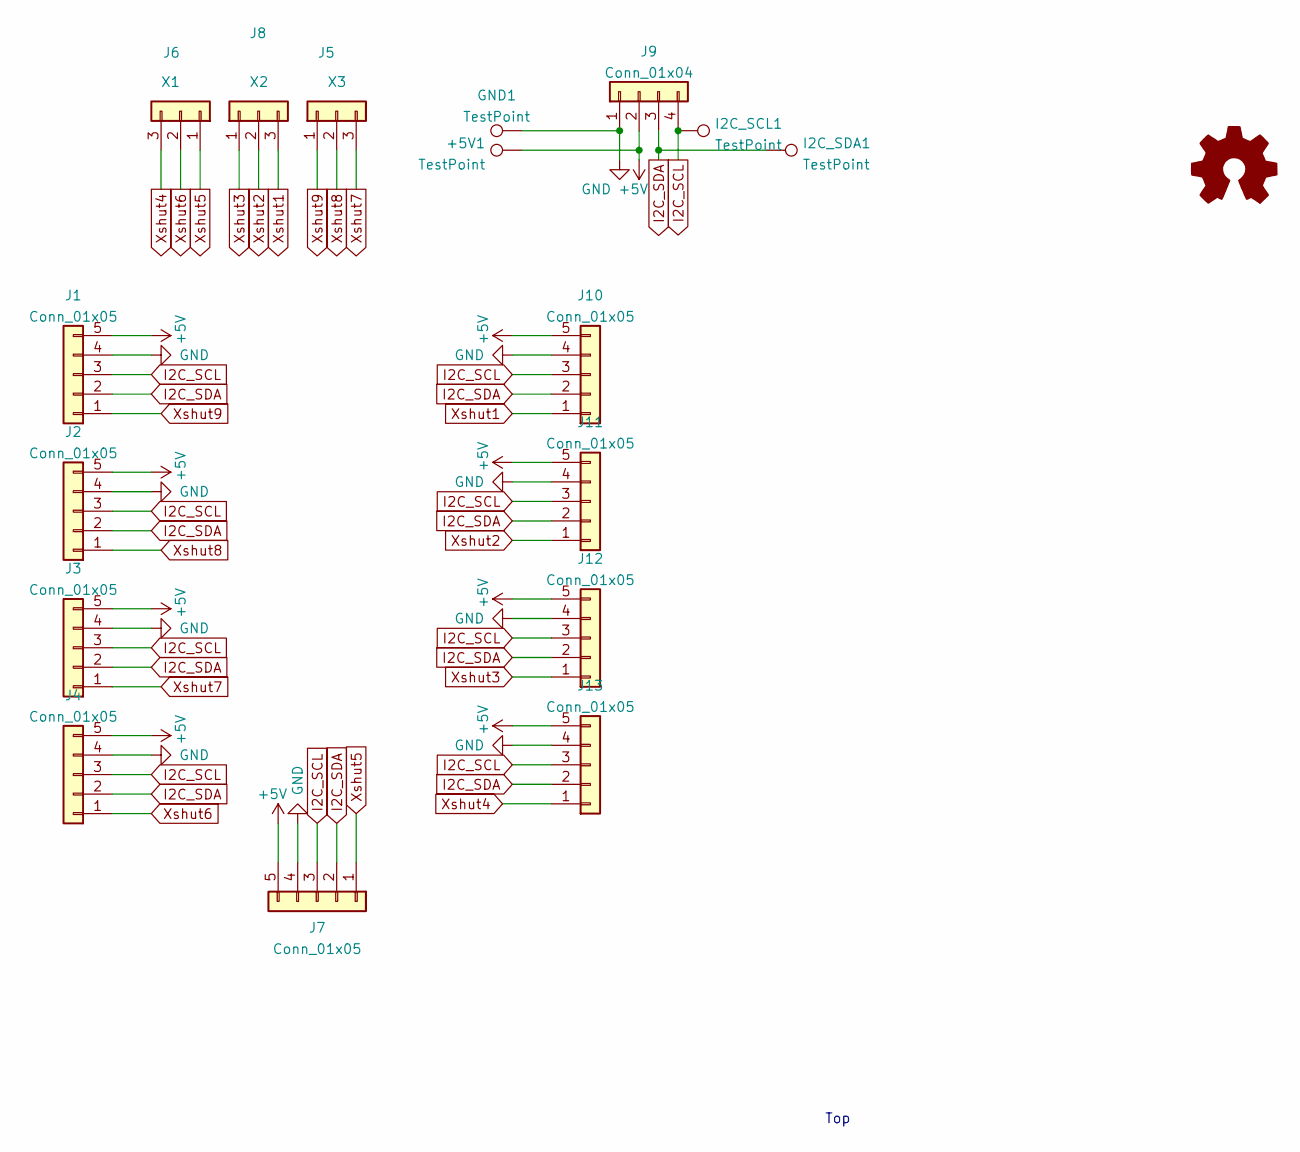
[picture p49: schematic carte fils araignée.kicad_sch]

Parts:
+5V1: TestPoint; TestPoint_Pad_D2.0mm
GND1: TestPoint; TestPoint_Pad_D2.0mm
I2C_SCL1, I2C_SDA1: TestPoint; TestPoint_Pad_D2.0mm
J1, J2, J3, J4, J10, J11, J12, J13: Conn_01x05; JST_EH_S5B-EH_1x05_P2.50mm_Horizontal
J5: X3; JST_EH_B3B-EH-A_1x03_P2.50mm_Vertical
J6: X1; JST_EH_B3B-EH-A_1x03_P2.50mm_Vertical
J7: Conn_01x05; JST_EH_B5B-EH-A_1x05_P2.50mm_Vertical
J8: X2; JST_EH_B3B-EH-A_1x03_P2.50mm_Vertical
J9: Conn_01x04; JST_EH_B4B-EH-A_1x04_P2.50mm_Vertical

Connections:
+5V: +5V1.1, J1.5, J2.5, J3.5, J4.5, J7.5, J9.2, J10.5, J11.5, J12.5, J13.5
GND: GND1.1, J1.4, J2.4, J3.4, J4.4, J7.4, J9.1, J10.4, J11.4, J12.4, J13.4
I2C_SCL: I2C_SCL1.1, J1.3, J2.3, J3.3, J4.3, J7.3, J9.4, J10.3, J11.3, J12.3, J13.3
I2C_SDA: I2C_SDA1.1, J1.2, J2.2, J3.2, J4.2, J7.2, J9.3, J10.2, J11.2, J12.2, J13.2
Xshut1: J8.3, J10.1
Xshut2: J8.2, J11.1
Xshut3: J8.1, J12.1
Xshut4: J6.3, J13.1
Xshut5: J6.1, J7.1
Xshut6: J4.1, J6.2
Xshut7: J3.1, J5.3
Xshut8: J2.1, J5.2
Xshut9: J1.1, J5.1

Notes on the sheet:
Top

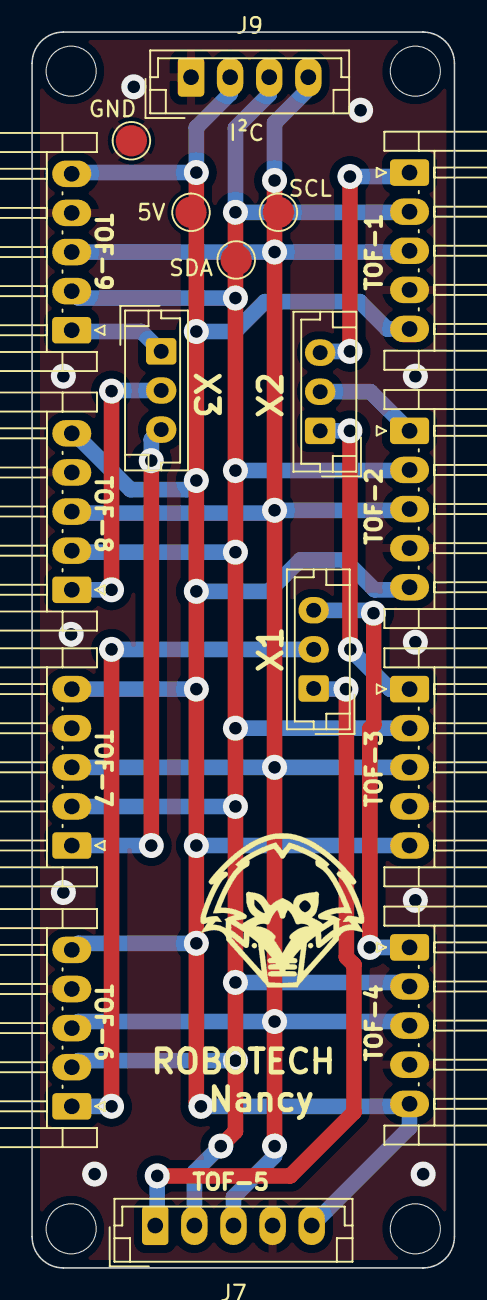
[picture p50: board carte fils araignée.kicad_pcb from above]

Board: 2 copper layers, 27.0 x 79.0 mm, 17 parts (0 on the bottom side), 13 nets.

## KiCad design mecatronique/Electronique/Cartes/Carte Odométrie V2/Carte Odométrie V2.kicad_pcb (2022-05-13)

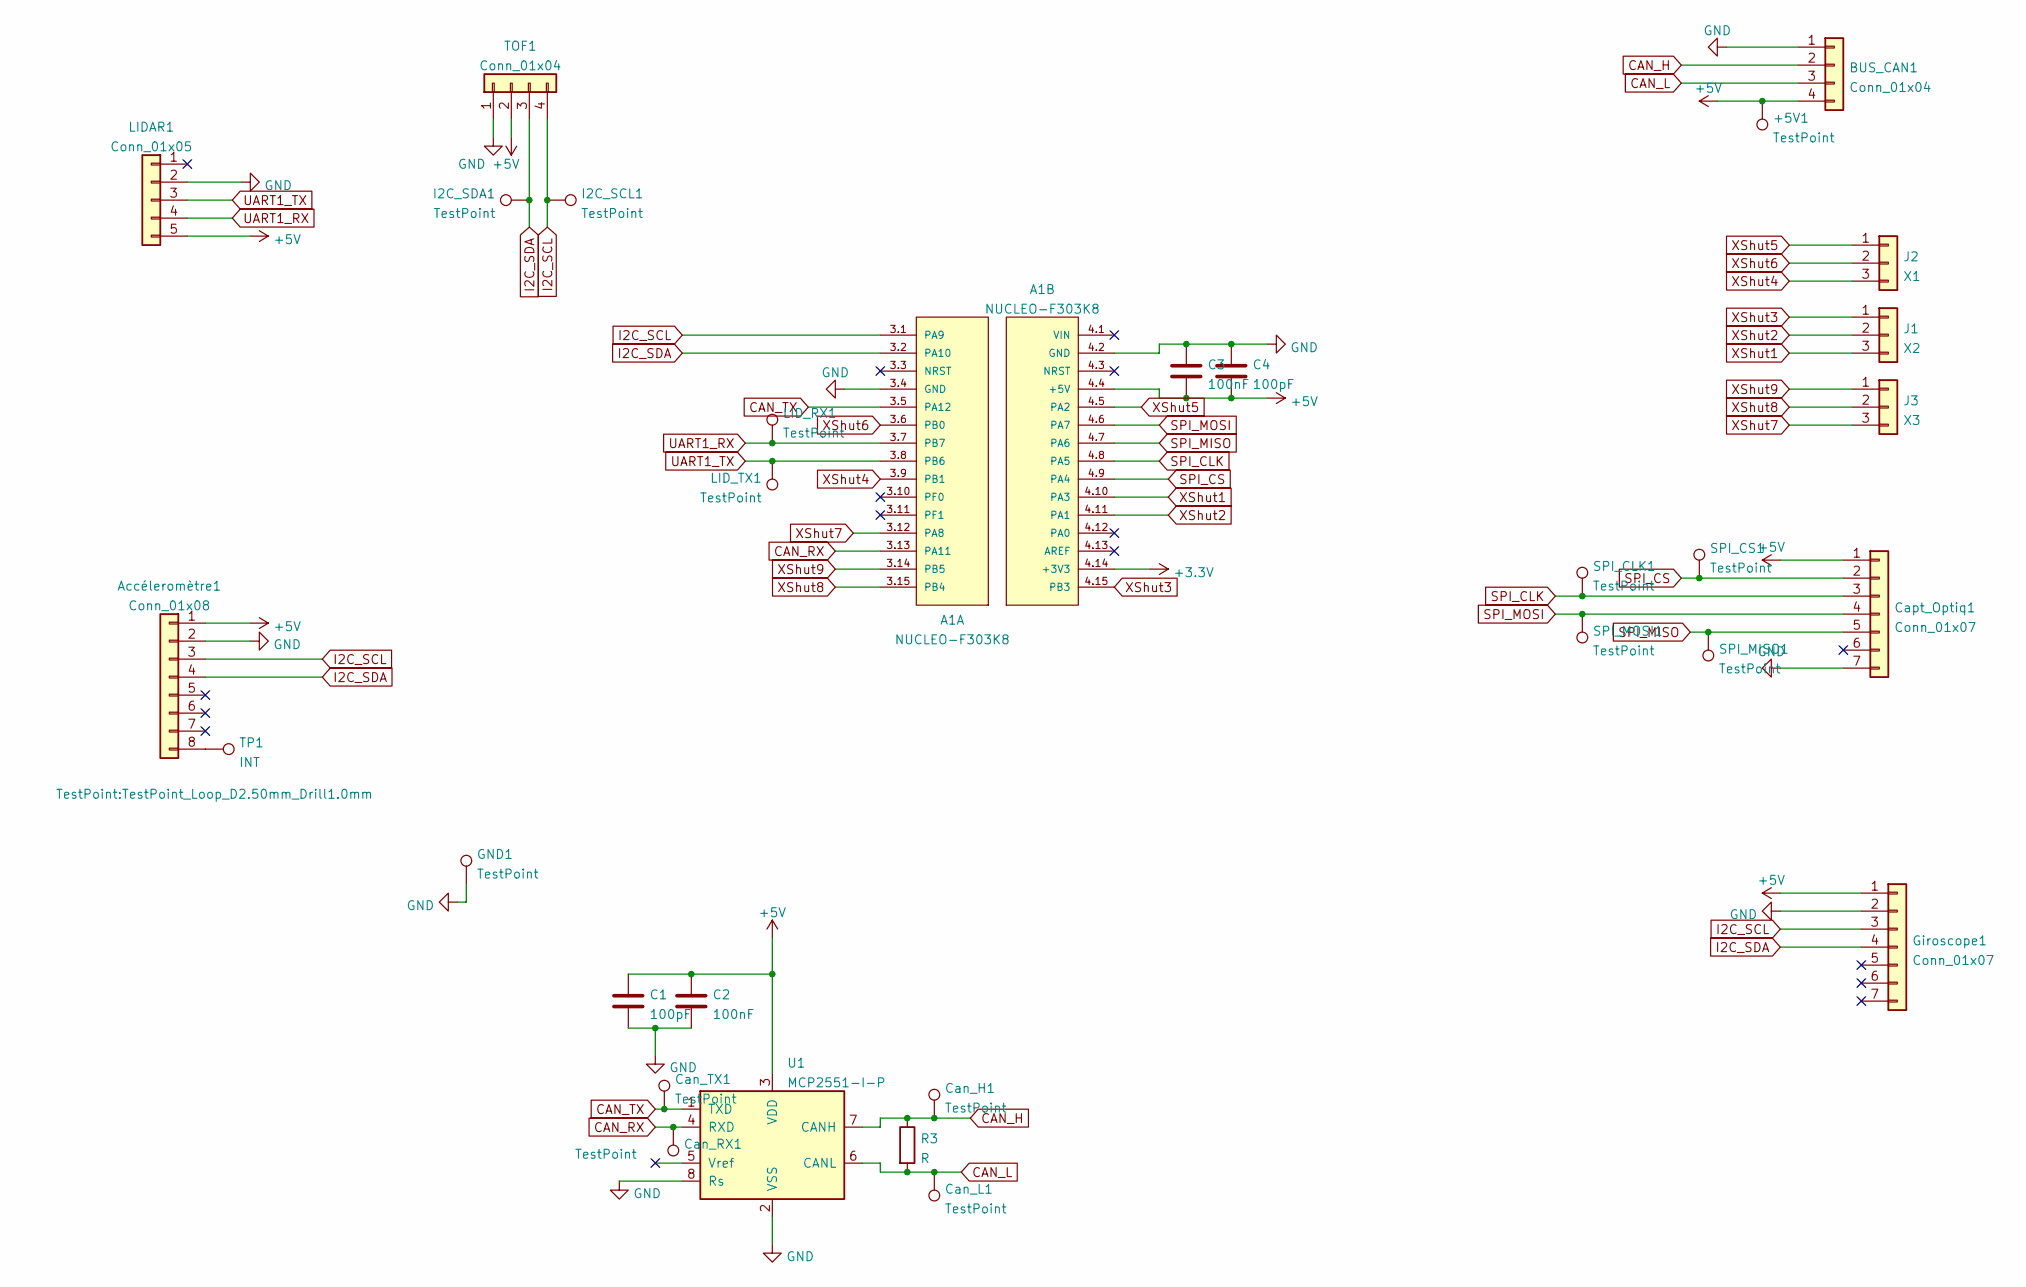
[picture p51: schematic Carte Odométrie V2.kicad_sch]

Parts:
+5V1: TestPoint; TestPoint_Pad_D2.0mm
A1: NUCLEO-F303K8; MODULE_NUCLEO-F303K8; PARTREV 3
Accéleromètre1: Conn_01x08; PinSocket_1x08_P2.54mm_Vertical
BUS_CAN1: Conn_01x04; JST_PH_B4B-PH-K_1x04_P2.00mm_Vertical
C1, C4: 100pF; C_1206_3216Metric
C2, C3: 100nF; C_1206_3216Metric
Can_H1: TestPoint; TestPoint_Pad_D2.0mm
Can_L1: TestPoint; TestPoint_Pad_D2.0mm
Can_RX1: TestPoint; TestPoint_Pad_D2.0mm
Can_TX1: TestPoint; TestPoint_Pad_D2.0mm
Capt_Optiq1: Conn_01x07; JST_PH_B7B-PH-K_1x07_P2.00mm_Vertical
GND1: TestPoint; TestPoint_Pad_D2.0mm
Giroscope1: Conn_01x07; PinSocket_1x07_P2.54mm_Vertical
I2C_SCL1, I2C_SDA1: TestPoint; TestPoint_Pad_D2.0mm
J1: X2; JST_EH_B3B-EH-A_1x03_P2.50mm_Vertical
J2: X1; JST_EH_B3B-EH-A_1x03_P2.50mm_Vertical
J3: X3; JST_EH_B3B-EH-A_1x03_P2.50mm_Vertical
LIDAR1: Conn_01x05; JST_PH_B5B-PH-K_1x05_P2.00mm_Vertical
LID_RX1: TestPoint; TestPoint_Pad_D2.0mm
LID_TX1: TestPoint; TestPoint_Pad_D2.0mm
R3: R; R_Axial_DIN0207_L6.3mm_D2.5mm_P10.16mm_Horizontal
SPI_CLK1: TestPoint; TestPoint_Pad_D2.0mm
SPI_CS1: TestPoint; TestPoint_Pad_D2.0mm
SPI_MISO1: TestPoint; TestPoint_Pad_D2.0mm
SPI_MOSI1: TestPoint; TestPoint_Pad_D2.0mm
TOF1: Conn_01x04; JST_PH_B4B-PH-K_1x04_P2.00mm_Vertical
TP1: INT; TestPoint_Loop_D2.50mm_Drill1.0mm
U1: MCP2551-I-P; DIP-8_W7.62mm

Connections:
+3V3: A1.4.14 (+3V3)
+5V: +5V1.1, A1.4.4 (+5V), Accéleromètre1.1, BUS_CAN1.4, C1.1, C2.1, C3.2, C4.2, Capt_Optiq1.1, Giroscope1.1, LIDAR1.5, TOF1.2, U1.3 (VDD)
CAN_H: BUS_CAN1.2, Can_H1.1, R3.1, U1.7 (CANH)
CAN_L: BUS_CAN1.3, Can_L1.1, R3.2, U1.6 (CANL)
CAN_RX: A1.3.13 (PA11), Can_RX1.1, U1.4 (RXD)
CAN_TX: A1.3.5 (PA12), Can_TX1.1, U1.1 (TXD)
GND: A1.3.4 (GND), A1.4.2 (GND), Accéleromètre1.2, BUS_CAN1.1, C1.2, C2.2, C3.1, C4.1, Capt_Optiq1.7, GND1.1, Giroscope1.2, LIDAR1.2, TOF1.1, U1.2 (VSS), U1.8 (Rs)
I2C_SCL: A1.3.1 (PA9), Accéleromètre1.3, Giroscope1.3, I2C_SCL1.1, TOF1.4
I2C_SDA: A1.3.2 (PA10), Accéleromètre1.4, Giroscope1.4, I2C_SDA1.1, TOF1.3
unnamed: Accéleromètre1.8, TP1.1
SPI_CLK: A1.4.8 (PA5), Capt_Optiq1.3, SPI_CLK1.1
SPI_CS: A1.4.9 (PA4), Capt_Optiq1.2, SPI_CS1.1
SPI_MISO: A1.4.7 (PA6), Capt_Optiq1.5, SPI_MISO1.1
SPI_MOSI: A1.4.6 (PA7), Capt_Optiq1.4, SPI_MOSI1.1
UART1_RX: A1.3.7 (PB7), LIDAR1.4, LID_RX1.1
UART1_TX: A1.3.8 (PB6), LIDAR1.3, LID_TX1.1
XShut1: A1.4.10 (PA3), J1.3
XShut2: A1.4.11 (PA1), J1.2
XShut3: A1.4.15 (PB3), J1.1
XShut4: A1.3.9 (PB1), J2.3
XShut5: A1.4.5 (PA2), J2.1
XShut6: A1.3.6 (PB0), J2.2
XShut7: A1.3.12 (PA8), J3.3
XShut8: A1.3.15 (PB4), J3.2
XShut9: A1.3.14 (PB5), J3.1

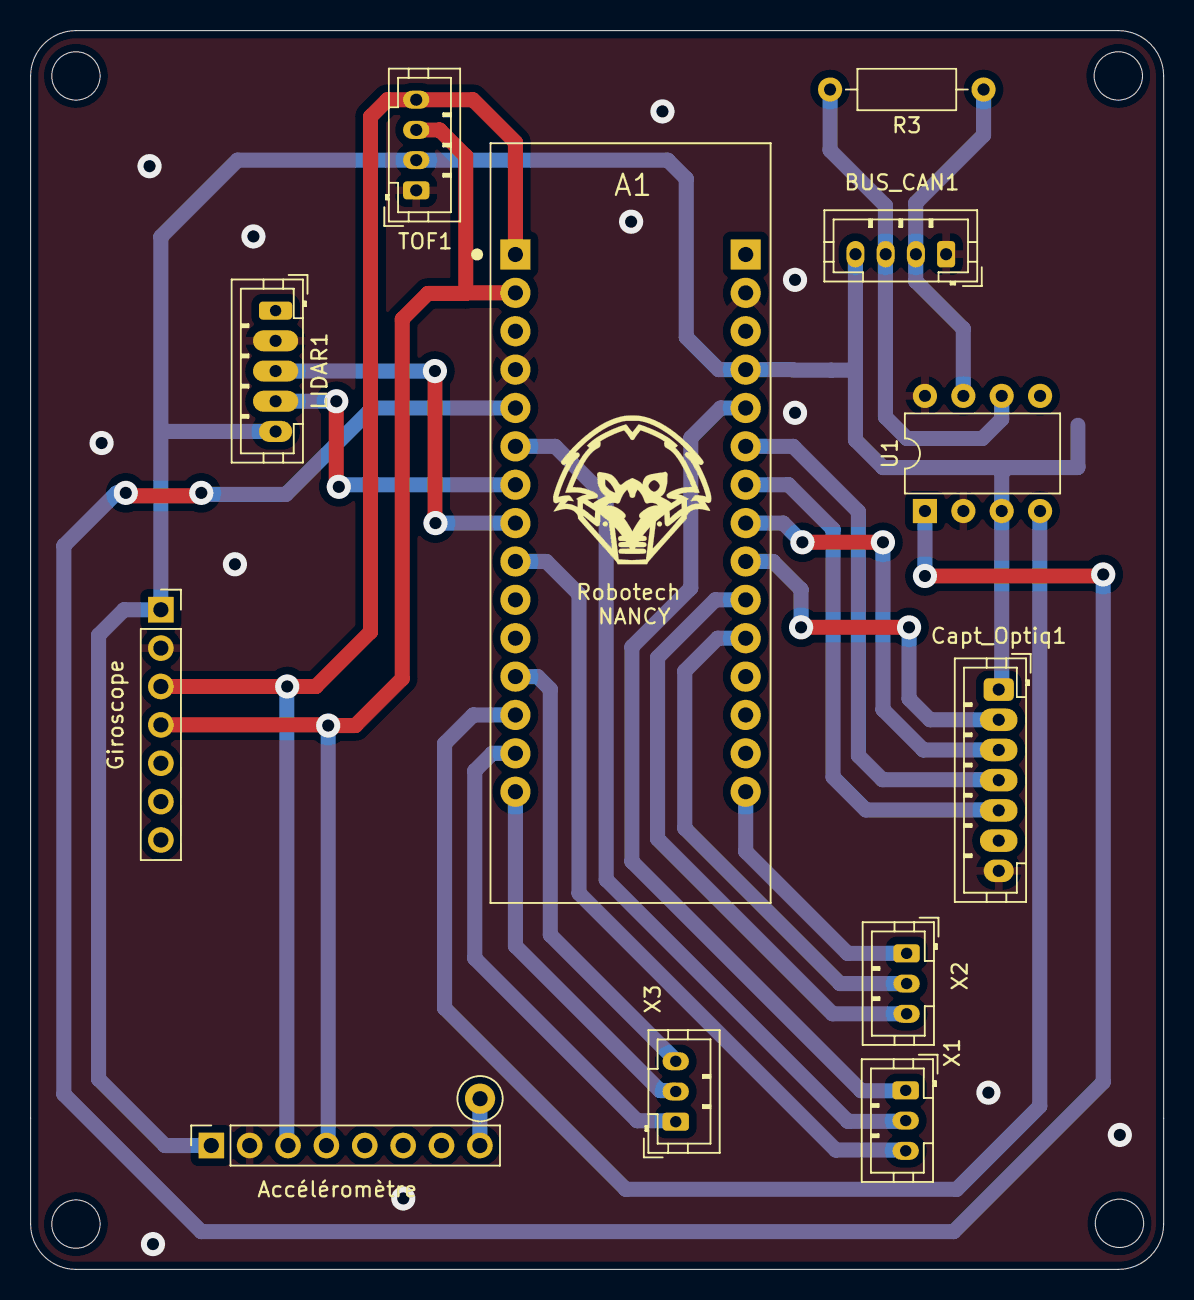
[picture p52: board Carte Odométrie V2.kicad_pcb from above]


Board: 2 copper layers, 75.0 x 82.0 mm, 35 parts (22 on the bottom side), 24 nets.

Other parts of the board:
REF: MountingHole_3.2mm_M3
REF#2, REF#3, REF#4: MountingHole_3.2mm_M3

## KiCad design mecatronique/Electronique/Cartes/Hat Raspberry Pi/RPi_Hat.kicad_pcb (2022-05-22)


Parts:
C1, C2: 100 nF; C_Disc_D5.1mm_W3.2mm_P5.00mm
C3, C4: 22 pF; C_Disc_D5.1mm_W3.2mm_P5.00mm
J1: Arrêt d'urgence; Hirose_DF11-6DP-2DSA_2x03_P2.00mm_Vertical
J2: RPi_GPIO; Pin_Header_Straight_2x20
J3: Goupille; JST_PH_B2B-PH-K_1x02_P2.00mm_Vertical
J4: Tension I2C; JST_PH_B2B-PH-K_1x02_P2.00mm_Vertical
J5: I2C; JST_PH_B4B-PH-K_1x04_P2.00mm_Vertical
R1: R; R_Axial_DIN0207_L6.3mm_D2.5mm_P2.54mm_Vertical
R2: 5k; R_Axial_DIN0207_L6.3mm_D2.5mm_P10.16mm_Horizontal
TP1, TP2, TP3, TP4, TP5, TP6, TP7, TP8, TP9, TP10, TP11, TP12, TP13, TP14: TestPoint; TestPoint_Pad_D1.0mm
TP15, TP16: TestPoint; TestPoint_Pad_D2.0mm
U1: XBee; XBEE-20_THT
U2: MCP25625-x-SS; SSOP-28_5.3x10.2mm_P0.65mm
Y1: 8MHz; Crystal_HC50_Horizontal

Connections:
+3.3VA: C1.2, J4.3, TP5.1, TP11.1, U1.1 (VCC), U2.1 (VIO), U2.19 (VDD); also elsewhere on the board
+5V: C2.1, J4.4, J5.2, R2.1, TP6.1, TP12.1, U2.27 (VDDA); also elsewhere on the board
/RPi_GPIO/BCM14_TXD: TP4.1, U1.3 (DIN); also elsewhere on the board
/RPi_GPIO/BCM15_RXD: TP3.1, U1.2 (DOUT); also elsewhere on the board
/RPi_GPIO/Starter: J3.2; also elsewhere on the board
/RPi_GPIO/cmd_relais_RPI: J1.2, TP2.1; also elsewhere on the board
CLK: TP7.1, U2.14 (SCK); also elsewhere on the board
CS: TP10.1, U2.17 (~CS); also elsewhere on the board
GND: C1.1, C2.2, C3.2, C4.2, J2.1, J3.1, J5.6, TP15.1, TP16.1, U1.10 (GND), U2.10 (GND), U2.26 (VSS); also elsewhere on the board
INT: U2.13 (~INT); also elsewhere on the board
MISO: TP9.1, U2.16 (SO); also elsewhere on the board
MOSI: TP8.1, U2.15 (SI); also elsewhere on the board
unnamed: C3.1, U2.8 (OSC2), Y1.1
unnamed: C4.1, U2.9 (OSC1), Y1.2
unnamed: J2.4, J4.1, J4.2
unnamed: R2.2, U2.18 (~RESET)
unnamed: TP13.1, U2.20 (TxCAN), U2.24 (TXD)
unnamed: TP14.1, U2.21 (RxCAN), U2.28 (RXD)
SCL: J2.2; also elsewhere on the board
SDA: J2.3; also elsewhere on the board
can_H: J5.1, R1.2, U2.4 (CANH)
can_L: J5.3, R1.1, U2.3 (CANL)
cmd_relais: J1.1, J5.4, TP1.1; also elsewhere on the board


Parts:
J6: Vcc I2C; PinHeader_2x02_P2.54mm_Vertical

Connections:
+3.3VA: J6.1 (3.3V); also elsewhere on the board
+5V: J6.2 (5V), J6.4 (5V); also elsewhere on the board
/RPi_GPIO/BCM14_TXD: J6.8 (BCM14_TXD); also elsewhere on the board
/RPi_GPIO/BCM15_RXD: J6.10 (BCM15_RXD); also elsewhere on the board
/RPi_GPIO/Starter: J6.29 (BCM5); also elsewhere on the board
/RPi_GPIO/cmd_relais_RPI: J6.15 (BCM22); also elsewhere on the board
CLK: J6.23 (BCM11_SCLK); also elsewhere on the board
CS: J6.24 (BCM8_CE0); also elsewhere on the board
GND: J6.6 (GND), J6.9 (GND), J6.25 (GND); also elsewhere on the board
INT: J6.22 (BCM25); also elsewhere on the board
MISO: J6.21 (BCM9_MISO); also elsewhere on the board
MOSI: J6.19 (BCM10_MOSI); also elsewhere on the board
SCL: J6.5 (BCM3_SCL); also elsewhere on the board
SDA: J6.3 (BCM2_SDA); also elsewhere on the board
cmd_relais: J6.13 (BCM27); also elsewhere on the board

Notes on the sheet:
Thru-Hole Connector



Board: 2 copper layers, 65.0 x 59.0 mm, 32 parts (6 on the bottom side), 23 nets.

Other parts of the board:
Test_INT: TestPoint_Pad_D1.0mm

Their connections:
INT: Test_INT.8; also elsewhere on the board

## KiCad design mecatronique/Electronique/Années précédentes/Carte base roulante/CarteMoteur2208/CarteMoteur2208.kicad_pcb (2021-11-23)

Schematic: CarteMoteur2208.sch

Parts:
C1, C2, C3, C4, C5, C6, C7, C8, C9, C10: 104; C_0603_1608Metric
C11: 106; C_0603_1608Metric
H1, H2, H3, H4: MountingHole_Pad; MountingHole_3.2mm_M3_Pad_Via
J1, J2: Conn_01x02; Molex_SPOX_5268-02A_1x02_P2.50mm_Horizontal
J3: Conn_02x03_Counter_Clockwise; Molex_Micro-Fit_3.0_43045-0600_2x03_P3.00mm_Horizontal
PROG1: STM32_SW; JTAG10
U1, U2: FXMA108; WQFN-20-1EP_2.5x4.5mm_P0.5mm_EP1x2.9mm
U3: STM32F103C8Tx; LQFP-48_7x7mm_P0.5mm
U4: TCAN337; SOIC-8_3.9x4.9mm_P1.27mm
U5: LT1117-3.3; SOT-223-3_TabPin2

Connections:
+3V3: C1.1, C2.1, C3.1, C4.1, C5.1, C6.1, C9.1, C11.1, PROG1.1, U1.1 (VCCA), U2.1 (VCCA), U3.9 (VDDA), U3.24 (VDD), U3.36 (VDD), U3.48 (VDD), U4.3 (VCC), U5.2 (VO)
+5V: C7.1, C8.1, C10.1, J3.1, U1.20 (VCCB), U2.20 (VCCB), U5.3 (VI); also elsewhere on the board
+BATT: J3.2, J3.3; also elsewhere on the board
/CAN_N: J1.2, J2.2, U4.6 (CANL)
/CAN_P: J1.1, J2.1, U4.7 (CANH)
/CAN_RX: U3.32 (PA11), U4.4 (RXD)
/CAN_TX: U3.33 (PA12), U4.1 (TXD)
/DIR1_H: U1.16 (B3); also elsewhere on the board
/DIR1_L: U1.5 (A3), U3.12 (PA2)
/DIR2_H: U1.19 (B0); also elsewhere on the board
/DIR2_L: U1.2 (A0), U3.15 (PA5)
/DIR3_H: U2.16 (B3); also elsewhere on the board
/DIR3_L: U2.5 (A3), U3.18 (PB0)
/DIR4_H: U2.19 (B0); also elsewhere on the board
/DIR4_L: U2.2 (A0), U3.21 (PB10)
/EN1_H: U1.14 (B5); also elsewhere on the board
/EN1_L: U1.7 (A5), U3.10 (PA0)
/EN2_H: U1.17 (B2); also elsewhere on the board
/EN2_L: U1.4 (A2), U3.13 (PA3)
/EN3_H: U2.14 (B5); also elsewhere on the board
/EN3_L: U2.7 (A5), U3.16 (PA6)
/EN4_H: U2.17 (B2); also elsewhere on the board
/EN4_L: U2.4 (A2), U3.19 (PB1)
/NRST: PROG1.10, U3.7 (NRST)
/STEP1_H: U1.15 (B4); also elsewhere on the board
/STEP1_L: U1.6 (A4), U3.11 (PA1)
/STEP2_H: U1.18 (B1); also elsewhere on the board
/STEP2_L: U1.3 (A1), U3.14 (PA4)
/STEP3_H: U2.15 (B4); also elsewhere on the board
/STEP3_L: U2.6 (A4), U3.17 (PA7)
/STEP4_H: U2.18 (B1); also elsewhere on the board
/STEP4_L: U2.3 (A1), U3.20 (PB2)
/SWCLK: PROG1.4, U3.37 (PA14)
/SWDIO: PROG1.2, U3.34 (PA13)
/SWO: PROG1.6, U3.38 (PA15)
GND: C1.2, C2.2, C3.2, C4.2, C5.2, C6.2, C7.2, C8.2, C9.2, C10.2, C11.2, H1.1, H2.1, H3.1, H4.1, J3.4, J3.5, J3.6, PROG1.3, PROG1.5, PROG1.9, U1.8 (A6), U1.9 (A7), U1.10 (GND), U1.11 (~OE), U2.8 (A6), U2.9 (A7), U2.10 (GND), U2.11 (~OE), U3.8 (VSSA), U3.23 (VSS), U3.35 (VSS), U3.47 (VSS), U4.2 (GND), U5.1 (GND); also elsewhere on the board

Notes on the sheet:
Drivers
Trous de montage
Interface CAN
Connecteurs
Adaptation de niveau logique
Régulation locale en 3.3V
Microcontrolleur
Carte Moteur TMC2208


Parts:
J4: Conn_01x04; Molex_Nano-Fit_105313-xx04_1x04_P2.50mm_Horizontal
U6: TMC2208; Pololu_Breakout-16_15.2x20.3mm

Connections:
+5V: U6.2 (VIO); also elsewhere on the board
+BATT: U6.8 (VM); also elsewhere on the board
/DIR1_H: U6.9 (DIR); also elsewhere on the board
/EN1_H: U6.16 (EN); also elsewhere on the board
/STEP1_H: U6.10 (STEP); also elsewhere on the board
GND: U6.1 (GND), U6.14 (MS2), U6.15 (MS1); also elsewhere on the board
unnamed: J4.1, U6.6 (M1B)
unnamed: J4.2, U6.5 (M1A)
unnamed: J4.3, U6.4 (M2A)
unnamed: J4.4, U6.3 (M2B)
unnamed: U6.11 (CLK), U6.12 (PDN)

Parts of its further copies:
J5, J6, J7: Conn_01x04; Molex_Nano-Fit_105313-xx04_1x04_P2.50mm_Horizontal
U7, U8, U9: TMC2208; Pololu_Breakout-16_15.2x20.3mm

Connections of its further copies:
+5V: U7.2 (VIO), U8.2 (VIO), U9.2 (VIO); also elsewhere on the board
+BATT: U7.8 (VM), U8.8 (VM), U9.8 (VM); also elsewhere on the board
/DIR2_H: U7.9 (DIR); also elsewhere on the board
/DIR3_H: U8.9 (DIR); also elsewhere on the board
/DIR4_H: U9.9 (DIR); also elsewhere on the board
/EN2_H: U7.16 (EN); also elsewhere on the board
/EN3_H: U8.16 (EN); also elsewhere on the board
/EN4_H: U9.16 (EN); also elsewhere on the board
/STEP2_H: U7.10 (STEP); also elsewhere on the board
/STEP3_H: U8.10 (STEP); also elsewhere on the board
/STEP4_H: U9.10 (STEP); also elsewhere on the board
GND: U7.1 (GND), U7.14 (MS2), U7.15 (MS1), U8.1 (GND), U8.14 (MS2), U8.15 (MS1), U9.1 (GND), U9.14 (MS2), U9.15 (MS1); also elsewhere on the board
unnamed: J5.1, U7.6 (M1B)
unnamed: J5.2, U7.5 (M1A)
unnamed: J5.3, U7.4 (M2A)
unnamed: J5.4, U7.3 (M2B)
unnamed: J6.1, U8.6 (M1B)
unnamed: J6.2, U8.5 (M1A)
unnamed: J6.3, U8.4 (M2A)
unnamed: J6.4, U8.3 (M2B)
unnamed: J7.1, U9.6 (M1B)
unnamed: J7.2, U9.5 (M1A)
unnamed: J7.3, U9.4 (M2A)
unnamed: J7.4, U9.3 (M2B)
unnamed: U7.11 (CLK), U7.12 (PDN)
unnamed: U8.11 (CLK), U8.12 (PDN)
unnamed: U9.11 (CLK), U9.12 (PDN)


Board: 2 copper layers, 100.0 x 55.0 mm, 32 parts (0 on the bottom side), 56 nets.

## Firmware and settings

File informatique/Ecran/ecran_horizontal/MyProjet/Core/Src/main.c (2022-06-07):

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

/* Includes ------------------------------------------------------------------*/
#include "main.h"
#include "cmsis_os.h"

/* USER CODE BEGIN Includes */
#include <stm32746g_discovery_qspi.h>
#include "PollingRoutines.h"
/* USER CODE END Includes */

/* USER CODE BEGIN PD */
#define REFRESH_COUNT        1835

#define SDRAM_TIMEOUT                            ((uint32_t)0xFFFF)
#define SDRAM_MODEREG_BURST_LENGTH_1             ((uint16_t)0x0000)
#define SDRAM_MODEREG_BURST_LENGTH_2             ((uint16_t)0x0001)
#define SDRAM_MODEREG_BURST_LENGTH_4             ((uint16_t)0x0002)
#define SDRAM_MODEREG_BURST_LENGTH_8             ((uint16_t)0x0004)
#define SDRAM_MODEREG_BURST_TYPE_SEQUENTIAL      ((uint16_t)0x0000)
#define SDRAM_MODEREG_BURST_TYPE_INTERLEAVED     ((uint16_t)0x0008)
#define SDRAM_MODEREG_CAS_LATENCY_2              ((uint16_t)0x0020)
#define SDRAM_MODEREG_CAS_LATENCY_3              ((uint16_t)0x0030)
#define SDRAM_MODEREG_OPERATING_MODE_STANDARD    ((uint16_t)0x0000)
#define SDRAM_MODEREG_WRITEBURST_MODE_PROGRAMMED ((uint16_t)0x0000)
#define SDRAM_MODEREG_WRITEBURST_MODE_SINGLE     ((uint16_t)0x0200)



/* USER CODE END PD */


CRC_HandleTypeDef hcrc;

DMA2D_HandleTypeDef hdma2d;

I2C_HandleTypeDef hi2c3;

LTDC_HandleTypeDef hltdc;

QSPI_HandleTypeDef hqspi;

UART_HandleTypeDef huart1;

SDRAM_HandleTypeDef hsdram1;

osThreadId defaultTaskHandHandle;
osThreadId taskUartMsgHandle;
osSemaphoreId binarySemUartMsgHandle;
/* USER CODE BEGIN PV */
static FMC_SDRAM_CommandTypeDef Command;
/* USER CODE END PV */

void SystemClock_Config(void);
static void MPU_Config(void);
static void MX_GPIO_Init(void);
static void MX_CRC_Init(void);
static void MX_QUADSPI_Init(void);
static void MX_DMA2D_Init(void);
static void MX_FMC_Init(void);
static void MX_LTDC_Init(void);
static void MX_I2C3_Init(void);
static void MX_USART1_UART_Init(void);
void StartDefaultTask(void const * argument);
void StartTaskUartMsg(void const * argument);

/**
  * @brief  The application entry point.
  * @retval int
  */
int main(void)
{
  /* MPU Configuration--------------------------------------------------------*/
  MPU_Config();

  /* Enable I-Cache---------------------------------------------------------*/
  SCB_EnableICache();

  /* Enable D-Cache---------------------------------------------------------*/
  SCB_EnableDCache();

  /* MCU Configuration--------------------------------------------------------*/

  /* Reset of all peripherals, Initializes the Flash interface and the Systick. */
  HAL_Init();

  /* Configure the system clock */
  SystemClock_Config();

  /* Initialize all configured peripherals */
  MX_GPIO_Init();
  MX_CRC_Init();
  MX_QUADSPI_Init();
  MX_DMA2D_Init();
  MX_FMC_Init();
  MX_LTDC_Init();
  MX_I2C3_Init();
  MX_USART1_UART_Init();
  /* USER CODE BEGIN RTOS_MUTEX */
  /* add mutexes, ... */
  /* USER CODE END RTOS_MUTEX */

  /* Create the semaphores(s) */
  /* definition and creation of binarySemUartMsg */
  osSemaphoreDef(binarySemUartMsg);
  binarySemUartMsgHandle = osSemaphoreCreate(osSemaphore(binarySemUartMsg), 1);

  /* USER CODE BEGIN RTOS_SEMAPHORES */
  /* add semaphores, ... */
  /* USER CODE END RTOS_SEMAPHORES */

  /* USER CODE BEGIN RTOS_TIMERS */
  /* start timers, add new ones, ... */
  /* USER CODE END RTOS_TIMERS */

  /* USER CODE BEGIN RTOS_QUEUES */
  /* add queues, ... */
  /* USER CODE END RTOS_QUEUES */

  /* Create the thread(s) */
  /* definition and creation of defaultTaskHand */
  osThreadDef(defaultTaskHand, StartDefaultTask, osPriorityNormal, 0, 4096);
  defaultTaskHandHandle = osThreadCreate(osThread(defaultTaskHand), NULL);

  /* definition and creation of taskUartMsg */
  osThreadDef(taskUartMsg, StartTaskUartMsg, osPriorityIdle, 0, 128);
  taskUartMsgHandle = osThreadCreate(osThread(taskUartMsg), NULL);

  /* USER CODE BEGIN RTOS_THREADS */
  /* add threads, ... */
  /* USER CODE END RTOS_THREADS */

  /* Start scheduler */
  osKernelStart();

  /* We should never get here as control is now taken by the scheduler */

  /* Infinite loop */
  /* USER CODE BEGIN WHILE */
  while (1)
  {
    /* USER CODE END WHILE */

    /* USER CODE BEGIN 3 */
  }
  /* USER CODE END 3 */
}

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
/* USER CODE BEGIN Header_StartDefaultTask */
/**
  * @brief  Function implementing the defaultTaskHand thread.
  * @param  argument: Not used 
  * @retval None
  */
/* USER CODE END Header_StartDefaultTask */
void StartDefaultTask(void const * argument)
{
  /* USER CODE BEGIN 5 */
  MX_TouchGFX_Process();
  /* Infinite loop */
  for(;;)
  {
    
    osDelay(1);
  }
  /* USER CODE END 5 */
}

/* USER CODE BEGIN Header_StartTaskUartMsg */
/**
* @brief Function implementing the taskUartMsg thread.
* @param argument: Not used
* @retval None
*/
/* USER CODE END Header_StartTaskUartMsg */
void StartTaskUartMsg(void const * argument)
{
  /* USER CODE BEGIN StartTaskUartMsg */
  PollingInit();
  /* Infinite loop */
  for(;;)
  {
	PollingRoutine();
    osDelay(1);
  }
  /* USER CODE END StartTaskUartMsg */
}

/* MPU Configuration */

void MPU_Config(void)
{
  MPU_Region_InitTypeDef MPU_InitStruct = {0};

  /* Disables the MPU */
  HAL_MPU_Disable();
  /** Initializes and configures the Region and the memory to be protected
  */
  MPU_InitStruct.Enable = MPU_REGION_ENABLE;
  MPU_InitStruct.Number = MPU_REGION_NUMBER0;
  MPU_InitStruct.BaseAddress = 0x90000000;
  MPU_InitStruct.Size = MPU_REGION_SIZE_256MB;
  MPU_InitStruct.SubRegionDisable = 0x0;
  MPU_InitStruct.TypeExtField = MPU_TEX_LEVEL0;
  MPU_InitStruct.AccessPermission = MPU_REGION_FULL_ACCESS;
  MPU_InitStruct.DisableExec = MPU_INSTRUCTION_ACCESS_ENABLE;
  MPU_InitStruct.IsShareable = MPU_ACCESS_NOT_SHAREABLE;
  MPU_InitStruct.IsCacheable = MPU_ACCESS_NOT_CACHEABLE;
  MPU_InitStruct.IsBufferable = MPU_ACCESS_NOT_BUFFERABLE;

  HAL_MPU_ConfigRegion(&MPU_InitStruct);
  /** Initializes and configures the Region and the memory to be protected
  */
  MPU_InitStruct.Enable = MPU_REGION_ENABLE;
  MPU_InitStruct.Number = MPU_REGION_NUMBER1;
  MPU_InitStruct.BaseAddress = 0x90000000;
  MPU_InitStruct.Size = MPU_REGION_SIZE_16MB;
  MPU_InitStruct.SubRegionDisable = 0x0;
  MPU_InitStruct.TypeExtField = MPU_TEX_LEVEL0;
  MPU_InitStruct.AccessPermission = MPU_REGION_FULL_ACCESS;
  MPU_InitStruct.DisableExec = MPU_INSTRUCTION_ACCESS_ENABLE;
  MPU_InitStruct.IsShareable = MPU_ACCESS_NOT_SHAREABLE;
  MPU_InitStruct.IsCacheable = MPU_ACCESS_CACHEABLE;
  MPU_InitStruct.IsBufferable = MPU_ACCESS_NOT_BUFFERABLE;

  HAL_MPU_ConfigRegion(&MPU_InitStruct);
  /* Enables the MPU */
  HAL_MPU_Enable(MPU_PRIVILEGED_DEFAULT);

}
/**
  * @brief  Period elapsed callback in non blocking mode
  * @note   This function is called  when TIM6 interrupt took place, inside
  * HAL_TIM_IRQHandler(). It makes a direct call to HAL_IncTick() to increment
  * a global variable "uwTick" used as application time base.
  * @param  htim : TIM handle
  * @retval None
  */
void HAL_TIM_PeriodElapsedCallback(TIM_HandleTypeDef *htim)
{
  if (htim->Instance == TIM6) {
    HAL_IncTick();
  }
}

/**
  * @brief  This function is executed in case of error occurrence.
  * @retval None
  */
void Error_Handler(void)
{
  /* USER CODE BEGIN Error_Handler_Debug */
  /* User can add his own implementation to report the HAL error return state */

  /* USER CODE END Error_Handler_Debug */
}

#ifdef  USE_FULL_ASSERT
/**
  * @brief  Reports the name of the source file and the source line number
  *         where the assert_param error has occurred.
  * @param  file: pointer to the source file name
  * @param  line: assert_param error line source number
  * @retval None
  */
void assert_failed(uint8_t *file, uint32_t line)
{
  /* USER CODE BEGIN 6 */
  /* User can add his own implementation to report the file name and line number,
     tex: printf("Wrong parameters value: file %s on line %d\r\n", file, line) */
  /* USER CODE END 6 */
}
#endif /* USE_FULL_ASSERT */

/************************ (C) COPYRIGHT STMicroelectronics *****END OF FILE****/

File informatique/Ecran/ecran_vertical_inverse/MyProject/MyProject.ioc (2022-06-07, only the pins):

Mcu.UserName=STM32F746NGHx
PA0/WKUP.GPIO_Label=ARDUINO A0
PA0/WKUP.Signal=ADCx_IN0
PA1.GPIO_Label=RMII_REF_CLK [LAN8742A-CZ-TR_REFCLK0]
PA1.Signal=ETH_REF_CLK
PA10.GPIO_Label=OTG_FS_ID
PA10.Signal=USB_OTG_FS_ID
PA11.GPIO_Label=OTG_FS_N
PA11.Signal=USB_OTG_FS_DM
PA12.GPIO_Label=OTG_FS_P
PA12.Signal=USB_OTG_FS_DP
PA13.GPIO_Label=SWDIO
PA13.Signal=SYS_JTMS-SWDIO
PA14.GPIO_Label=SWCLK
PA14.Signal=SYS_JTCK-SWCLK
PA15.GPIO_Label=ARDUINO PWM/D9
PA15.Signal=S_TIM2_CH1_ETR
PA2.GPIO_Label=RMII_MDIO [LAN8742A-CZ-TR_MDIO]
PA2.Signal=ETH_MDIO
PA3.GPIO_Label=ULPI_D0 [USB3320C-EZK_D0]
PA3.Signal=USB_OTG_HS_ULPI_D0
PA4.GPIO_Label=DCMI_HSYNC
PA4.Signal=DCMI_HSYNC
PA5.GPIO_Label=ULPI_CLK [USB3320C-EZK_CLKOUT]
PA5.Signal=USB_OTG_HS_ULPI_CK
PA6.Signal=DCMI_PIXCLK
PA7.GPIO_Label=RMII_CRS_DV [LAN8742A-CZ-TR_CRS_DV]
PA7.Signal=ETH_CRS_DV
PA8.GPIO_Label=ARDUINO PWM/D10
PA8.Signal=S_TIM1_CH1
PA9.GPIO_Label=VCP_TX [STM32F103CBT6_PA3]
PA9.Signal=USART1_TX
PB0.GPIO_Label=ULPI_D1 [USB3320C-EZK_D1]
PB0.Signal=USB_OTG_HS_ULPI_D1
PB1.GPIO_Label=ULPI_D2 [USB3320C-EZK_D2]
PB1.Signal=USB_OTG_HS_ULPI_D2
PB10.GPIO_Label=ULPI_D3 [USB3320C-EZK_D3]
PB10.Signal=USB_OTG_HS_ULPI_D3
PB11.GPIO_Label=ULPI_D4 [USB3320C-EZK_D4]
PB11.Signal=USB_OTG_HS_ULPI_D4
PB12.GPIO_Label=ULPI_D5 [USB3320C-EZK_D5]
PB12.Signal=USB_OTG_HS_ULPI_D5
PB13.GPIO_Label=ULPI_D6 [USB3320C-EZK_D6]
PB13.Signal=USB_OTG_HS_ULPI_D6
PB14.GPIO_Label=ARDUINO MISO/D12
PB14.Signal=SPI2_MISO
PB15.GPIO_Label=ARDUINO MOSI/PWM/D11
PB15.Signal=SPI2_MOSI
PB2.Signal=QUADSPI_CLK
PB3.GPIO_Label=SWO
PB3.Signal=SYS_JTDO-SWO
PB4.GPIO_Label=ARDUINO PWM/D3
PB4.Signal=S_TIM3_CH1
PB5.GPIO_Label=ULPI_D7 [USB3320C-EZK_D7]
PB5.Signal=USB_OTG_HS_ULPI_D7
PB6.GPIO_Label=QSPI_NCS [N25Q128A13EF840E_S]
PB6.Signal=QUADSPI_BK1_NCS
PB7.GPIO_Label=VCP_RX [STM32F103CBT6_PA2]
PB7.Signal=USART1_RX
PB8.GPIO_Label=ARDUINO SCL/D15
PB8.Signal=I2C1_SCL
PB9.GPIO_Label=ARDUINO SDA/D14
PB9.Signal=I2C1_SDA
PC0.GPIO_Label=ULPI_STP [USB3320C-EZK_STP]
PC0.Signal=USB_OTG_HS_ULPI_STP
PC1.GPIO_Label=RMII_MDC [LAN8742A-CZ-TR_MDC]
PC1.Signal=ETH_MDC
PC10.GPIO_Label=SDMMC_D2
PC10.Signal=SDMMC1_D2
PC11.GPIO_Label=SDMMC_D3
PC11.Signal=SDMMC1_D3
PC12.GPIO_Label=SDMMC_CK
PC12.Signal=SDMMC1_CK
PC13.GPIO_Label=uSD_Detect
PC13.Signal=GPIO_Input
PC14/OSC32_IN.GPIO_Label=RCC_OSC32_IN
PC14/OSC32_IN.Signal=RCC_OSC32_IN
PC15/OSC32_OUT.GPIO_Label=RCC_OSC32_OUT
PC15/OSC32_OUT.Signal=RCC_OSC32_OUT
PC2.GPIO_Label=ULPI_DIR [USB3320C-EZK_DIR]
PC2.Signal=USB_OTG_HS_ULPI_DIR
PC3.GPIO_Label=FMC_SDCKE0 [MT48LC4M32B2B5-6A_CKE]
PC3.Signal=FMC_SDCKE0
PC4.GPIO_Label=RMII_RXD0 [LAN8742A-CZ-TR_RXD0]
PC4.Signal=ETH_RXD0
PC5.GPIO_Label=RMII_RXD1 [LAN8742A-CZ-TR_RXD1]
PC5.Signal=ETH_RXD1
PC6.GPIO_Label=ARDUINO TX/D1
PC6.Signal=USART6_TX
PC7.GPIO_Label=ARDUINO RX/D0
PC7.Signal=USART6_RX
PC8.Signal=SDMMC1_D0
PC9.Signal=SDMMC1_D1
PD0.GPIO_Label=FMC_D2 [MT48LC4M32B2B5-6A_DQ2]
PD0.Signal=FMC_D2_DA2
PD1.GPIO_Label=FMC_D3 [MT48LC4M32B2B5-6A_DQ3]
PD1.Signal=FMC_D3_DA3
PD10.GPIO_Label=FMC_D15 [MT48LC4M32B2B5-6A_DQ15]
PD10.Signal=FMC_D15_DA15
PD11.GPIO_Label=QSPI_D0 [N25Q128A13EF840E_DQ0]
PD11.Signal=QUADSPI_BK1_IO0
PD12.GPIO_Label=QSPI_D1 [N25Q128A13EF840E_DQ1]
PD12.Signal=QUADSPI_BK1_IO1
PD13.GPIO_Label=QSPI_D3 [N25Q128A13EF840E_DQ3]
PD13.Signal=QUADSPI_BK1_IO3
PD14.GPIO_Label=FMC_D0 [MT48LC4M32B2B5-6A_DQ0]
PD14.Signal=FMC_D0_DA0
PD15.GPIO_Label=FMC_D1 [MT48LC4M32B2B5-6A_DQ1]
PD15.Signal=FMC_D1_DA1
PD2.GPIO_Label=SDMMC_CMD
PD2.Signal=SDMMC1_CMD
PD3.GPIO_Label=DCMI_D5
PD3.Signal=DCMI_D5
PD4.GPIO_Label=OTG_FS_OverCurrent [STMPS2141STR_Fault]
PD4.Signal=GPIO_Input
PD5.GPIO_Label=OTG_FS_PowerSwitchOn [STMPS2141STR_EN]
PD5.Signal=GPIO_Output
PD6.GPIO_Label=Audio_INT
PD6.Signal=GPXTI6
PD7.GPIO_Label=SPDIF_RX0 [74LVC1G04SE_4]
PD7.Signal=SPDIFRX_IN0
PD8.GPIO_Label=FMC_D13 [MT48LC4M32B2B5-6A_DQ13]
PD8.Signal=FMC_D13_DA13
PD9.GPIO_Label=FMC_D14 [MT48LC4M32B2B5-6A_DQ14]
PD9.Signal=FMC_D14_DA14
PE0.GPIO_Label=FMC_NBL0 [MT48LC4M32B2B5-6A_DQM0]
PE0.Signal=FMC_NBL0
PE1.GPIO_Label=FMC_NBL1 [MT48LC4M32B2B5-6A_DQM1]
PE1.Signal=FMC_NBL1
PE10.GPIO_Label=FMC_D7 [MT48LC4M32B2B5-6A_DQ7]
PE10.Signal=FMC_D7_DA7
PE11.GPIO_Label=FMC_D8 [MT48LC4M32B2B5-6A_DQ8]
PE11.Signal=FMC_D8_DA8
PE12.GPIO_Label=FMC_D9 [MT48LC4M32B2B5-6A_DQ9]
PE12.Signal=FMC_D9_DA9
PE13.GPIO_Label=FMC_D10 [MT48LC4M32B2B5-6A_DQ10]
PE13.Signal=FMC_D10_DA10
PE14.GPIO_Label=FMC_D11 [MT48LC4M32B2B5-6A_DQ11]
PE14.Signal=FMC_D11_DA11
PE15.GPIO_Label=FMC_D12 [MT48LC4M32B2B5-6A_DQ12]
PE15.Signal=FMC_D12_DA12
PE2.GPIO_Label=QSPI_D2 [N25Q128A13EF840E_DQ2]
PE2.Signal=QUADSPI_BK1_IO2
PE3.GPIO_Label=OTG_HS_OverCurrent [STMPS2151STR_FAULT]
PE3.Signal=GPIO_Input
PE4.GPIO_Label=LCD_B0 [RK043FN48H-CT672B_B0]
PE4.Signal=LTDC_B0
PE5.GPIO_Label=DCMI_D6
PE5.Signal=DCMI_D6
PE6.GPIO_Label=DCMI_D7
PE6.Signal=DCMI_D7
PE7.GPIO_Label=FMC_D4 [MT48LC4M32B2B5-6A_DQ4]
PE7.Signal=FMC_D4_DA4
PE8.GPIO_Label=FMC_D5 [MT48LC4M32B2B5-6A_DQ5]
PE8.Signal=FMC_D5_DA5
PE9.GPIO_Label=FMC_D6 [MT48LC4M32B2B5-6A_DQ6]
PE9.Signal=FMC_D6_DA6
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

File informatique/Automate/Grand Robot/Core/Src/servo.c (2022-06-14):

/*
 * servo.c
 *
 *  Created on: May 10, 2022
 *      Author: thibault
 */

#include "servo.h"
#include "actionneurs_define.h"
extern TIM_HandleTypeDef htim1;
extern TIM_HandleTypeDef htim3;
extern TIM_HandleTypeDef htim6;

/*
 * @brief démarre le servomoteur (l'axe est éteint et relaché par défaut)
 * @retval None
 */
void servo1Start() {
	HAL_TIM_PWM_Start(&htim3, TIM_CHANNEL_4);
}

/*
 * @brief éteint le servomoteur
 * @retval None
 */
void servo1Stop() {
	HAL_TIM_PWM_Stop(&htim3, TIM_CHANNEL_4);
}

/*
 * @brief démarre le servomoteur (l'axe est éteint et relaché par défaut)
 * @retval None
 */
void servo2Start() {
	HAL_TIMEx_PWMN_Start(&htim1, TIM_CHANNEL_3);
}

/*
 * @brief éteint le servomoteur
 * @retval None
 */
void servo2Stop() {
	HAL_TIMEx_PWMN_Stop(&htim1, TIM_CHANNEL_3);

}

/*
 * @brief deplace le servo moteur à l'angle indiqué
 * @param angle en entier et en degré que l'ont veut déplacer le servomoteur
 * @retval renvoie un entier 1 pour valider le deplacement du  servomoteur
 */
int deplacement_servo_ventouse(int angle) {
	servo1Start();

	TIM3-> CCR4=ANGLE_VENTOUSE_REFERENCE-angle*PAS_SERVO_VENTOUSE;
	attendre(TEMPS_ACTION_VENTOUSE);
	servo1Stop();
	return 1;
}

/*
 * @brief deplace le servo moteur à l'angle indiqué
 * @param angle en entier et en degré que l'ont veut déplacer le servomoteur
 * @retval renvoie un entier 1 pour valider le deplacement du  servomoteur
 */
int deplacement_servo_courroie(int angle) {
	servo2Start();

	TIM1-> CCR3=ANGLE_COURROIE_REFERENCE-angle*PAS_SERVO_COURROIE;
	attendre(TEMPS_ACTION_COURROIE);
	servo2Stop();
	return 1;
}

/*
 * @brief implémente un delay sans utiliser la fonctione HAL_DELAY de stm qu'il ne faut pas utiliser
 * @retval None
 */
void attendre(int temps){ //temps en ms durant lequel la commande reste active
	HAL_TIM_Base_Start(&htim6);
	uint32_t start = __HAL_TIM_GET_COUNTER(&htim6);
	//uint32_t start=HAL_GetTick();

	while((__HAL_TIM_GET_COUNTER(&htim6)-start)<temps) {
	//	while((HAL_GetTick()-start)<temps) {
		}
}

/*
 * @brief active la pompe
 * @retval 0 lorsque l'action est terminée et que la pompe est activé
 */
int pompe_on() {
	HAL_GPIO_WritePin(pompe_GPIO_Port, pompe_Pin, RESET); //modifie la valeur du pin a 0 pour activer la pompe
	return 0;
}

/*
 * @brief désactive la pompe
 * @retval 0 lorsque l'action est terminée et que la pompe est désactivé
 */
int pompe_off() {
	HAL_GPIO_WritePin(pompe_GPIO_Port, pompe_Pin, SET);  //modifie la valeur du pin a 1 pour activer la pompe
	return 0;
}

/*
 * @brief regroupe les 2 fonctione précedente pour activer/désactiver la pompe
 * @param bool 1 allume la pompe et 0 éteint la pompe
 * @retval bool 0 si la pompe à bien été eteint, 1 si la pompe à bien été allumé
 */
uint8_t pompe(bool ordre) {
	if (ordre==ON) {
		pompe_on();
		return 1;
	}
	else if (ordre==OFF) {
		pompe_off();
		return 0;
	}
	else {

	}
}

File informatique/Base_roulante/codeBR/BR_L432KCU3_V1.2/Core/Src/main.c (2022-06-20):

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
/* Includes ------------------------------------------------------------------*/
#include "main.h"

/* USER CODE BEGIN Includes */
#include <stdbool.h>
#define _USE_MATH_DEFINES // for C
#include <math.h>

#include "stm32l4xx_it.h" /*!< Fonctions d'interruptions */
#include "defineMotor.h"
#include "variable.h" /* Initialisation des variables */
#include "deplacement.h" /* Fonction deplacement */
#include "motor.h" /*!< Fonctions des moteurs */
#include "defineCan.h"
#include "can.h"
/* USER CODE END Includes */

 CAN_HandleTypeDef hcan1;

TIM_HandleTypeDef htim1;
DMA_HandleTypeDef hdma_tim1_up;

/* USER CODE BEGIN PV */
CAN_HandleTypeDef hcan_p;
uint8_t CanAdresse;


Motor_t motor1 = {
	.cnt = 0,
	.diviseur = 0,
	.DIAMETRE = DIAMETRE_ROUE * COEFF_DIAMETRE_1,
	.STEP_SIZE = (float)(360) / (float)(DIV_DRIVER_1 * 200),

	.PIN_STEP = STEP_M1_Pin,
	.PIN_DIR = DIR_M1_Pin,
	.PIN_STEP_TYPE = STEP_M1_GPIO_Port,
	.PIN_DIR_TYPE = DIR_M1_GPIO_Port,
	.pinStepState = RESET,
	.pinDirState = RESET,
};

Motor_t motor2 = {
	.cnt = 0,
	.diviseur = 0,
	.DIAMETRE = DIAMETRE_ROUE * COEFF_DIAMETRE_2,
	.STEP_SIZE = (float)(360) / (float)(DIV_DRIVER_2 * 200),

	.PIN_STEP = STEP_M2_Pin,
	.PIN_DIR = DIR_M2_Pin,
	.PIN_STEP_TYPE = STEP_M2_GPIO_Port,
	.PIN_DIR_TYPE = DIR_M2_GPIO_Port,
	.pinStepState = RESET,
	.pinDirState = RESET,
};

Motor_t motor3 = {
	.cnt = 0,
	.diviseur = 0,
	.DIAMETRE = DIAMETRE_ROUE * COEFF_DIAMETRE_3,
	.STEP_SIZE = (float)(360) / (float)(DIV_DRIVER_3 * 200),

	.PIN_STEP = STEP_M3_Pin,
	.PIN_DIR = DIR_M3_Pin,
	.PIN_STEP_TYPE = STEP_M3_GPIO_Port,
	.PIN_DIR_TYPE = DIR_M3_GPIO_Port,
	.pinStepState = RESET,
	.pinDirState = RESET,
};



/* USER CODE END PV */

void SystemClock_Config(void);
static void MX_GPIO_Init(void);
static void MX_DMA_Init(void);
static void MX_TIM1_Init(void);
static void MX_CAN1_Init(void);
/**
  * @brief  The application entry point.
  * @retval int
  */
int main(void)
{
  /* MCU Configuration--------------------------------------------------------*/

  /* Reset of all peripherals, Initializes the Flash interface and the Systick. */
  HAL_Init();

  /* Configure the system clock */
  SystemClock_Config();

  /* Initialize all configured peripherals */
  MX_GPIO_Init();
  MX_DMA_Init();
  MX_TIM1_Init();
  MX_CAN1_Init();
  /* USER CODE BEGIN 2 */

  CAN_Config(hcan1, CAN_ADDR_BASE_ROULANTE_E);

  /* USER CODE END 2 */

  /*
   * @brief clampe les moteurs et active les demi-steps
   */
  motor_en(RESET); //RESET = actif
  motor_micro_step(SET, RESET); //1/2 step

  /* Infinite loop */
  /* USER CODE BEGIN WHILE */
  while (1)
  {
    /* USER CODE END WHILE */
	/* USER CODE BEGIN 3 */
  }
  /* USER CODE END 3 */
}

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


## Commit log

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2021-11-23 Transfert
    Transfert des anciens documents utiles
    [CAN_EXT.sch, Carte d'alimentation.kicad_pcb, Carte d'alimentation.sch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]
2021-11-26 Réorganiation
    Réorganisation de l'architecture électrique et des fichiers du github
    [Carte mesure courant.kicad_pcb, Carte mesure courant.sch]
2021-11-30 Début carte d'alimentation
    [Alimentation.kicad_pcb, Alimentation.sch]
2021-11-30 Update alim
    [Alimentation.kicad_pcb, Alimentation.sch]
2021-12-14 Update Alim
    Manque fusible
    [Alimentation.kicad_pcb]
2022-01-05 Update Alim
    Transistor alimenté en 12V
    [Alimentation.kicad_pcb, Alimentation.kicad_sch]
2022-01-11 Carte odométrie v2
    [Carte Odométrie V2.kicad_pcb, Carte Odométrie V2.kicad_sch, Carte Odométrie V2.sch]
2022-01-11 Ajout HAT RPI
    [Alimentation.kicad_pcb, Alimentation.kicad_sch, RPi_GPIO.kicad_sch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]
2022-01-17 Update
    Update archi, hat et alim
    [RPi_Hat.kicad_pcb, RPi_Hat.kicad_sch, xbee.kicad_sch]
2022-01-17 Revert "Carte odométrie v2"
    This reverts commit 187b49f128330c4b72c5874e322502618ae8852e.
    [Carte Odométrie V2.kicad_pcb, Carte Odométrie V2.kicad_sch, Carte Odométrie V2.sch]
2022-01-17 Revert "Update"
    This reverts commit 5fda5d97c123c8007ff4d0ab26b634aa447f3b27.
    [RPi_Hat.kicad_pcb, RPi_Hat.kicad_sch, xbee.kicad_sch]
2022-01-17 Update Carte Odométrie
    [Carte Odométrie V2.kicad_pcb]
2022-01-17 Revert "Ajout HAT RPI"
    This reverts commit 37495a5355fe7fea7368fed2234a493909df8e69.
    [Alimentation.kicad_pcb, Alimentation.kicad_sch, RPi_GPIO.kicad_sch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]
2022-01-17 Reprise backup
    [RPi_Hat.kicad_pcb, RPi_Hat.kicad_sch, xbee.kicad_sch]
2022-01-17 carte odométrie avec resistance pull up
    [Carte Odométrie V2.kicad_pcb, Carte Odométrie V2.kicad_sch]
2022-01-17 Carte odométrie v2 "fini"
    [Carte Odométrie V2.kicad_pcb, Carte Odométrie V2.kicad_sch]
2022-01-17 Update HAT RPI
    - Ajout MCP25625
    [RPi_GPIO.kicad_sch, RPi_Hat.kicad_sch]
2022-01-17 Réparation sync
    [RPi_Hat.sch]
2022-01-17 carte transceiver base roulante
    [Transceiver Base Roulante.kicad_pcb, Transceiver Base Roulante.kicad_sch]
2022-01-17 Update HAT
    [RPi_GPIO.kicad_sch, RPi_Hat.kicad_pcb, RPi_Hat.kicad_sch]
2022-01-18 Carte transceiver base roulante update
    [Transceiver Base Roulante.kicad_pcb]
2022-01-18 Excel Inventaire et Commande
    [Commande groupée Mecatronique.ods, Inventaire pour les 2 robots.ods]
2022-01-19 Update HAT + commande
    [Alimentation.kicad_pcb, RPi_Hat.kicad_pcb]
2022-01-19 Résolution warning HAT
    [RPi_Hat.kicad_pcb]
2022-01-19 TCAN base roulante update
    [Transceiver Base Roulante.kicad_pcb]
2022-01-20 Résolution des problèmes du HAT
    [RPi_Hat.kicad_pcb]
2022-01-21 Update alim sécurité
    [Alimentation.kicad_pcb, Alimentation.kicad_sch]
2022-01-21 Update alim
    Corrections pistes et via
    Merci Hugo et Francois
    [RPi_Hat.kicad_pcb, RPi_Hat.kicad_sch]
2022-01-21 Update alim correction
    [RPi_GPIO.kicad_sch, RPi_Hat.kicad_pcb, RPi_Hat.kicad_sch]
2022-01-25 Update HAT
    - Ajout des pads
    - Correction du schéma
    - Corrections diverses
    [RPi_GPIO.kicad_sch, RPi_Hat.kicad_pcb, RPi_Hat.kicad_sch]
2022-01-28 Update HAT & Archi
    HAT : - Ajout de l'interrupteur logique de démarrage
    Archi : - Update générale
    [RPi_GPIO.kicad_sch, RPi_Hat.kicad_pcb, RPi_Hat.kicad_sch]
2022-01-28 Rangement et update pour les années pro
    [Commande 2eme robot.ods]
2022-01-29 Correction de petites fautes
2022-01-29 Update Alim
    Fusible
    [Alimentation.kicad_pcb, Alimentation.kicad_sch]
2022-02-01 Update Alim
    Changement des dimensions
    [Alimentation.kicad_pcb]
2022-02-01 Ajout image soutenance
    [RPi_Hat.kicad_pcb, RPi_Hat.kicad_sch]
2022-02-01 Carte Bras test Résistance
    [Carte Bras petit Robot V2couche.kicad_pcb, Carte Bras petit Robot V2couche.kicad_sch, Carte Bras petit Robot.kicad_sch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]
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2022-02-21 correctifs xbee
    Committer: Samuel-Charles DITTE-DESTREE <samueldittedestree@protonmail.com>
    [main.cpp]
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2022-03-02 Update fabrication
    Pistes et pastilles plus larges
    [Alimentation.kicad_pcb, RPi_Hat.kicad_pcb]
2022-03-06 Update alim
    - Ajout de la connexion du bus can à la BR
    - Normalisation des perçages
    [Alimentation-B_Cu.gbr, Alimentation-Edge_Cuts.gbr, Alimentation-F_Cu.gbr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]
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2022-03-15 Update random
    [RPi_Hat-B_Cu.gbr, RPi_Hat-Edge_Cuts.gbr, RPi_Hat-F_Cu.gbr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]
2022-03-29 Update BR et alim
    - Mise à jour BR pour 2022 (taille de piste, modèle 3D ...)
    - Changements mineurs sur l'alim
    [Shield BR.kicad_pcb, Shield BR.kicad_sch, TCAN332D.step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]
2022-03-29 Update BR
    - Avancement raccords EN/MS1/MS2
    [RPi_Hat.kicad_sch, Shield BR.kicad_pcb, Shield BR.kicad_sch]
2022-04-05 Updates mineurs
    [Shield BR.kicad_pcb]
2022-04-05 Update BR
    [RPi_Hat.kicad_pcb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]
2022-04-20 Udpate HAT
    Sérigraphie
    Points de tests
    Arret d'urgence
    I2C
    [RPi_GPIO.kicad_sch, RPi_Hat.kicad_pcb, RPi_Hat.kicad_sch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]
2022-04-24 Correction pcb BR
    [Alimentation.kicad_pcb, Alimentation.kicad_sch, RPi_Hat.kicad_pcb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]
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2022-05-03 maj final carte normalement
    [Carte Actionneur petit robot JLC PCB.kicad_pcb, Carte Actionneur petit robot JLC PCB.kicad_sch, Carte Bras ENORME Robot.kicad_pcb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]
2022-05-07 Ajout points de masse
    [Alimentation.kicad_pcb, Alimentation.kicad_sch, Shield BR.kicad_pcb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]
2022-05-08 Ajout des cartes actionneurs corrigées
    [Carte Actionneur petit robot JLC PCB.kicad_pcb, Carte Actionneur petit robot JLC PCB.kicad_sch, Carte Bras ENORME Robot.kicad_pcb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]
2022-05-08 Update actionneur grand robot
    Ajout d'une 2e empreinte avec détrompeur
    [Carte Actionneur petit robot JLC PCB.kicad_pcb, Carte Actionneur petit robot JLC PCB.kicad_sch, Carte Bras ENORME Robot.kicad_pcb]
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2022-05-09 Normalisation des trous
    Alim
    Hat
    BR
    Act G
    Act P
    [Alimentation.csv, Alimentation.kicad_pcb, BOM.xlsx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]
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2022-05-09 Update BOM
    Pas encore finit
    [BOM.xlsx, Carte Odométrie V2.kicad_sch]
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2022-05-11 Fix plan de masse grand robot
    [BOM.xlsx, Carte Bras ENORME Robot.kicad_pcb, Carte Odométrie V2.kicad_pcb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]
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2022-05-11 Update Araignée & Odométrie
    [Carte Odométrie V2.kicad_pcb, Carte Odométrie V2.kicad_sch, carte fils araignée.kicad_pcb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]
2022-05-13 Corrections d'erreurs TOF et GYROSCOPE
    [TOF_SAM.ioc, main.c, main.h]
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2022-05-13 Correction Carte Alim
    [Alimentation.kicad_pcb, Alimentation.kicad_sch]
2022-05-13 correction carte bras gros robot
    [Carte Bras ENORME Robot.kicad_pcb, Carte Bras ENORME Robot.kicad_sch]
2022-05-13 Correction carte araignée
    [carte fils araignée.kicad_pcb, carte fils araignée.kicad_sch]
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2022-05-31 ajout des codes SAM
    [texts.xlsx]
2022-05-31 Random bullsit go brrrrr
    [Carte Actionneur petit robot JLC PCB.kicad_sch]
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2022-06-14 git fix
    [L432KC_save_can Debug.cfg, canV2 Debug.cfg, texts.xlsx]
2022-06-14 fix git
    [Alimentation-B_Cu.gbr, Alimentation-CuBottom.gbr, Alimentation-CuTop.gbr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]
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

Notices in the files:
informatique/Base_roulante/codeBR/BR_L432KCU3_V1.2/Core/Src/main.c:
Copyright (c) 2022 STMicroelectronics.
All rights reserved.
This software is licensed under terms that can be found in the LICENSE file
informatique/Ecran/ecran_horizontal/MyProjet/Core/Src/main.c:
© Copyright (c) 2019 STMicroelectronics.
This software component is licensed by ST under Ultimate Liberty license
